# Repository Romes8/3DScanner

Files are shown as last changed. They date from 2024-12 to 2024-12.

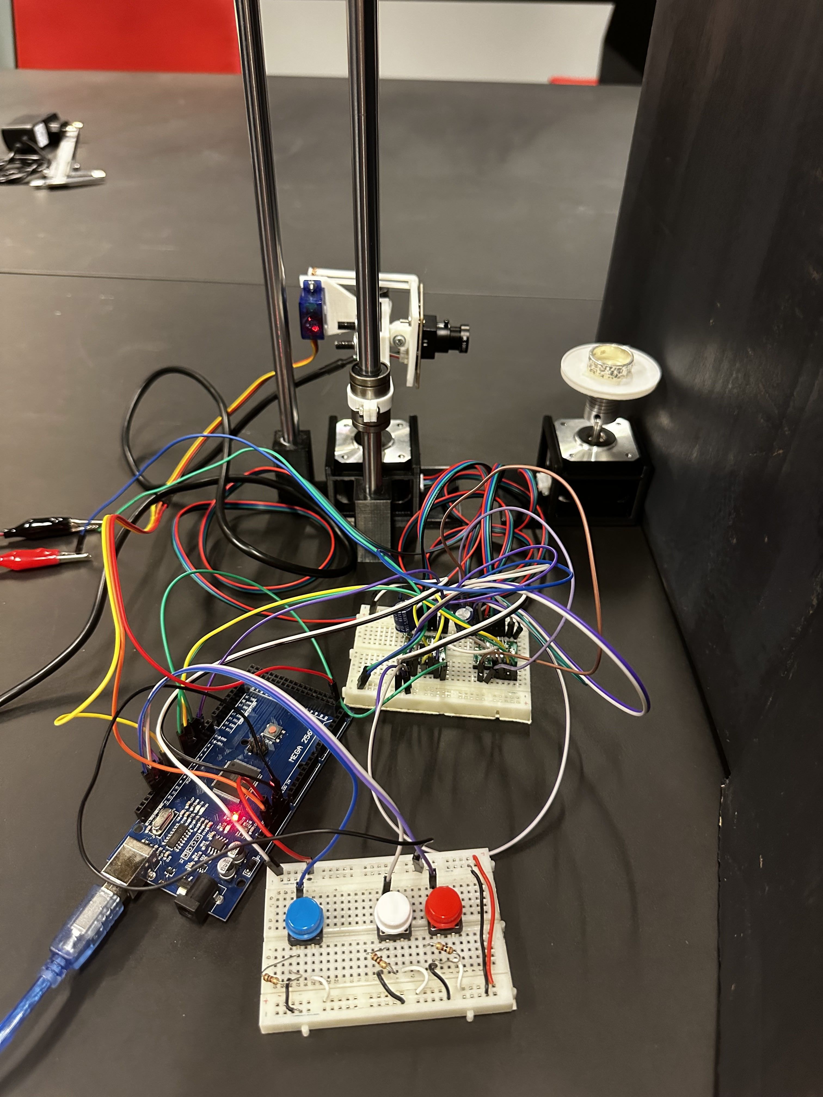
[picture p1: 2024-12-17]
device_images/IMG_8125.jpg

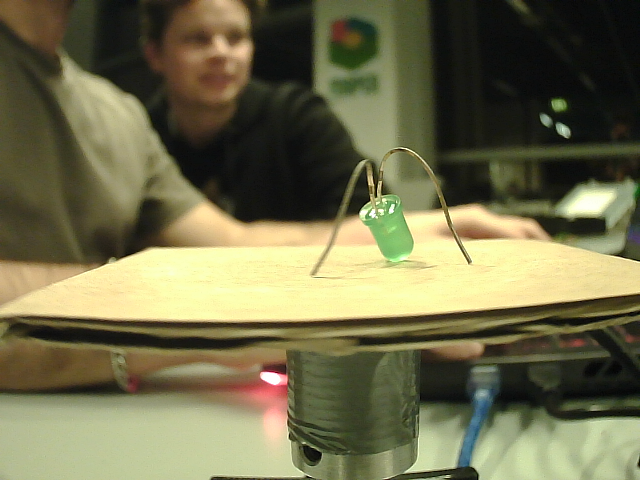
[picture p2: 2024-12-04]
scanned_images/LED/image_20241126-172908.png

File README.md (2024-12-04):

# 3DScanner
Final project for HTMAA 2024  
Overleft report link - https://www.overleaf.com/project/673f16d9a8e7cf6065c0855a

The primary objective of our project, was to design and create a small scale, portable plug and play small scale 3D model scanner. The motivation to create this stems fromour personal interest in 3D printing and miniature models. This paper outlines the steps taken to achieve our goal, discussing different aspects such as the requirements, mechanics, electronics and software used. The results present a successfully designed and executed 3D scanner that was able to scan and reproduce a 3D object.

# How to run 

1. Upload the code into the Arduino using Arduino IDE
2. Turn on "Camera app" on your device
3. Use buttons on the 3DScanner to set the initial scanning position. Adjust the distance to focus on the object
4. Turn off the "camera app"
5. Turn on the camera.py scrpit. Run this in CMD with admin permissions
6. Press the start button on 3D Scanner
7. Verify that the machine starts to move and images are being saved into folder where camera.py script is being saved. 
8. Wait until the 3D Scanner finishes - approx. 8,5 min

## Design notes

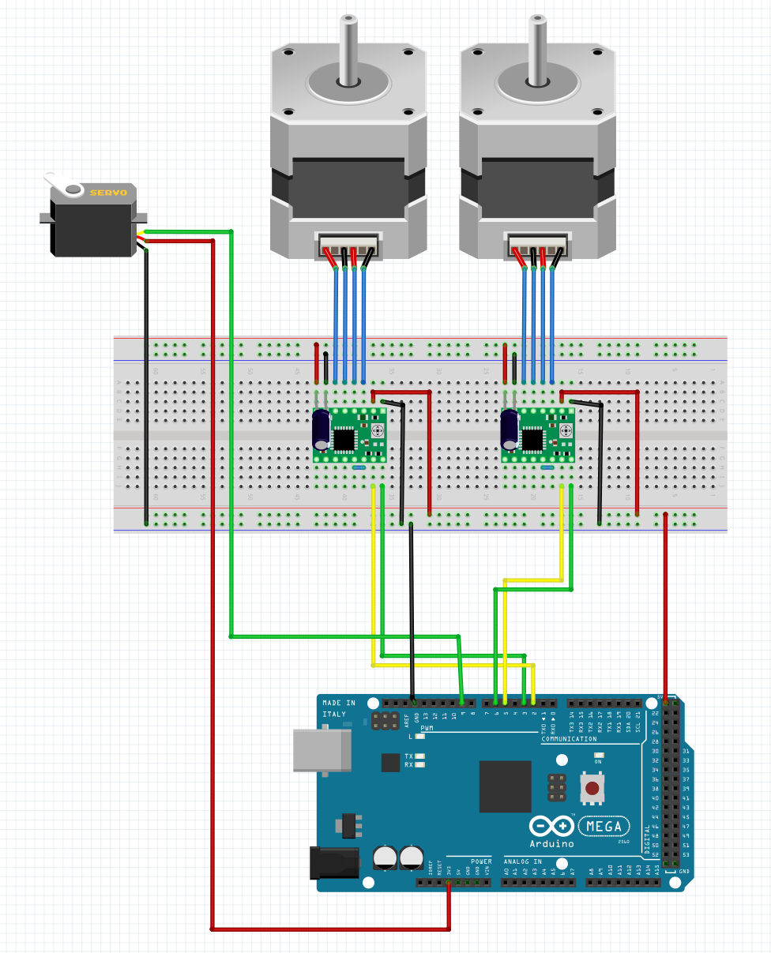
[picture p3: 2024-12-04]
technical_images/arduinoSchematic-scanner.png

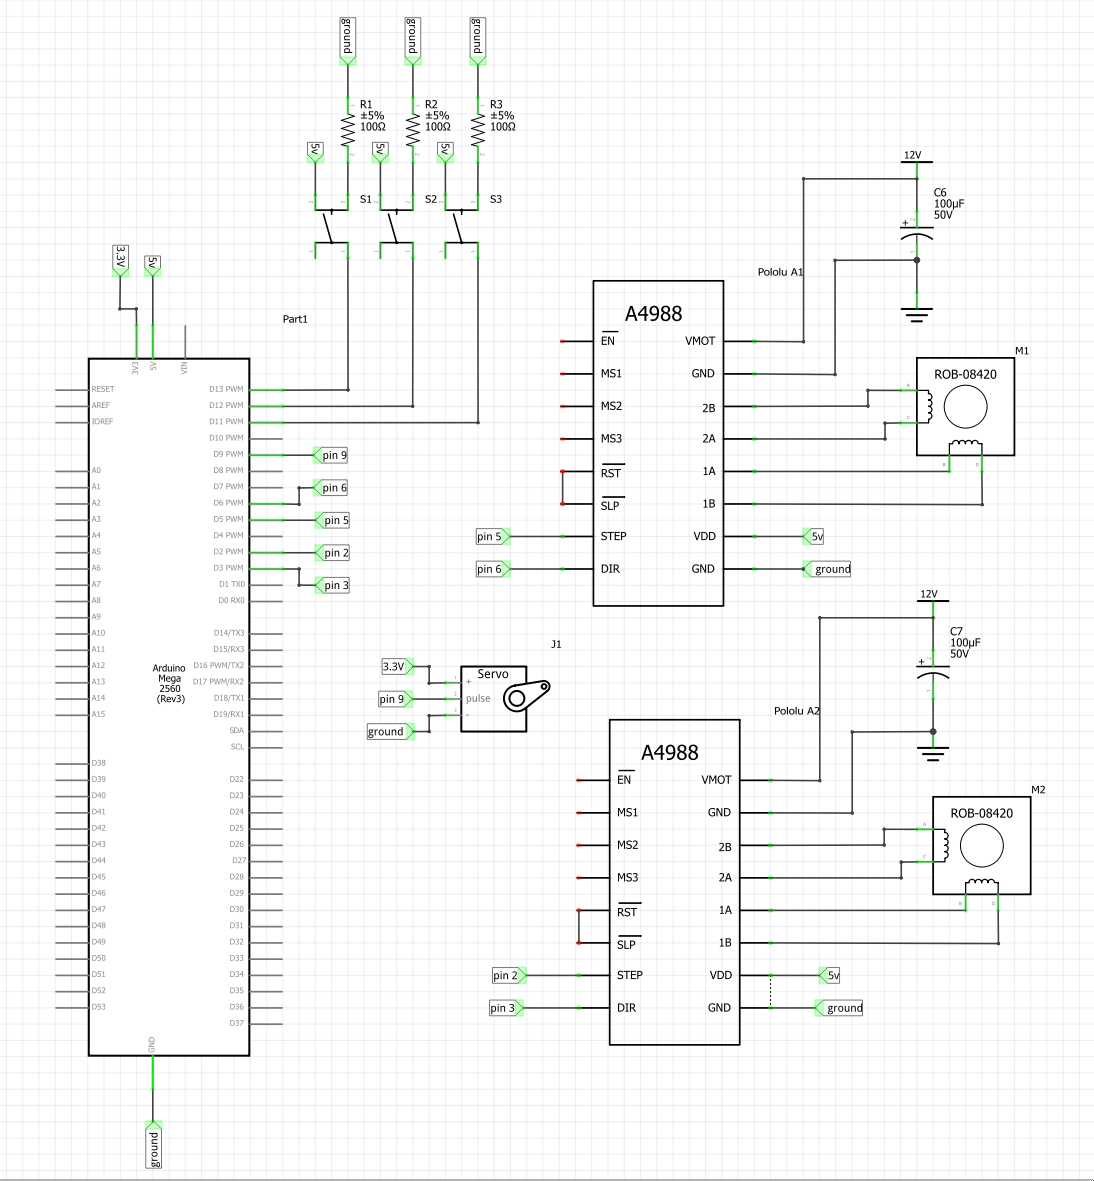
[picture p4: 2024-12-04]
technical_images/schematic-scanner.png

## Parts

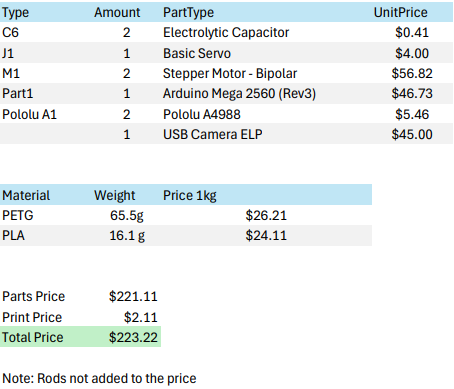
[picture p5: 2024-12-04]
technical_images/BOM-3DScanner.png

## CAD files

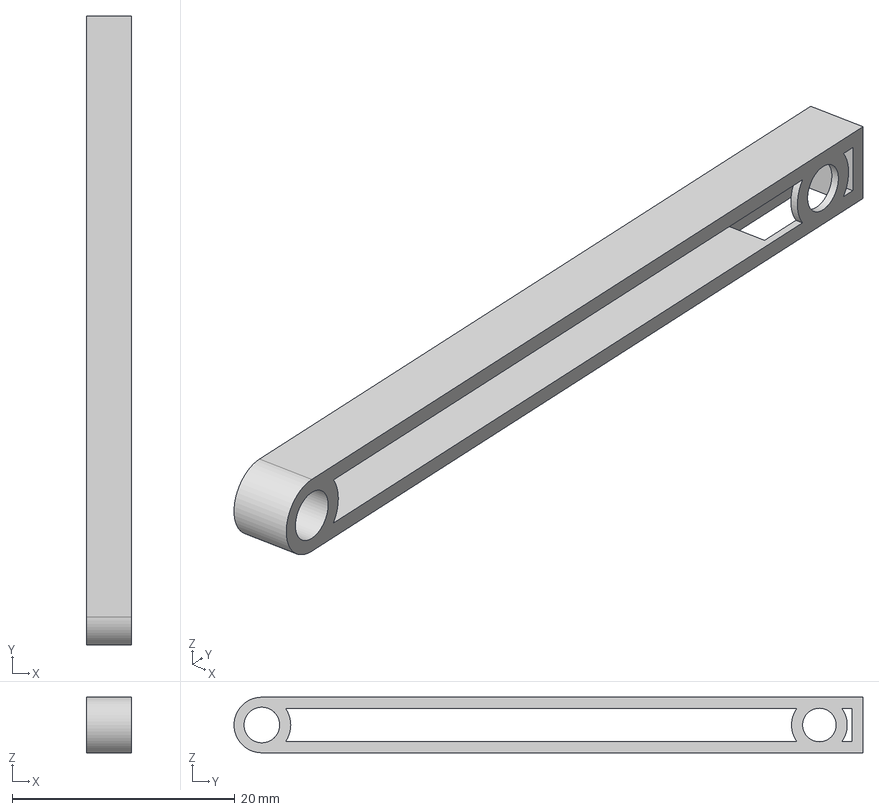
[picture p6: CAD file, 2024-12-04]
3Dmodels/TiltingRod.step
4.00 x 56.5 x 5.00 mm

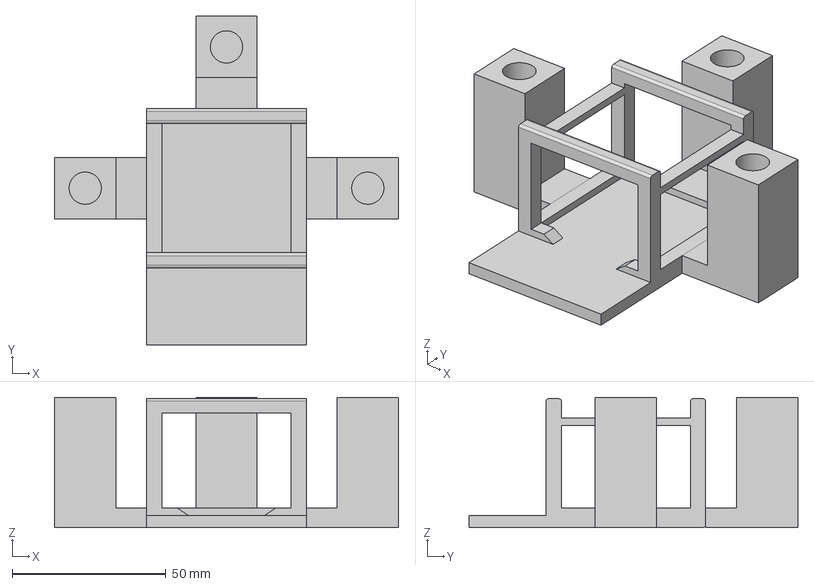
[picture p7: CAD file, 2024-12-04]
3Dmodels/Right motor holderv2.step
112.0 x 107.0 x 42.3 mm

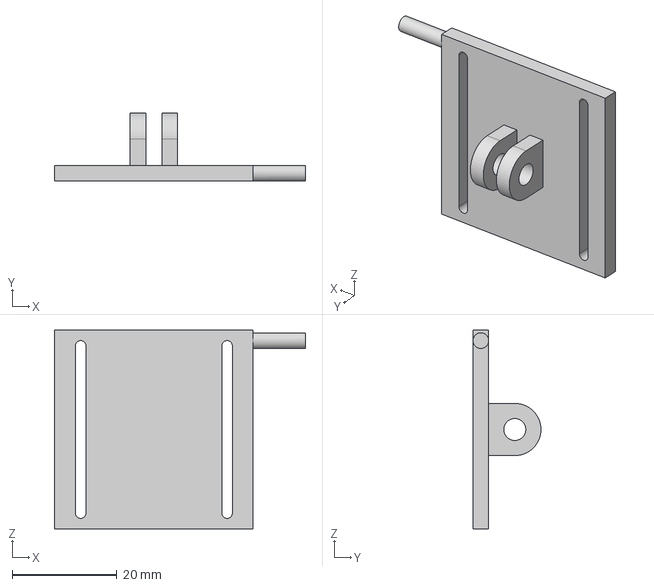
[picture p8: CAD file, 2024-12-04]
3Dmodels/CameraHolder.step
48.0 x 13.0 x 38.0 mm

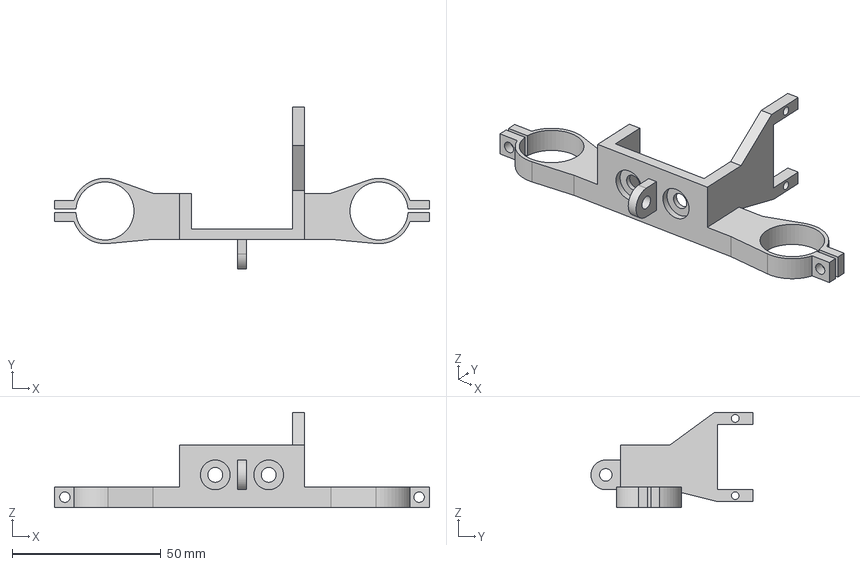
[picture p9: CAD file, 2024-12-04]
3Dmodels/CameraHolderBase.step
126.1 x 54.5 x 32.0 mm

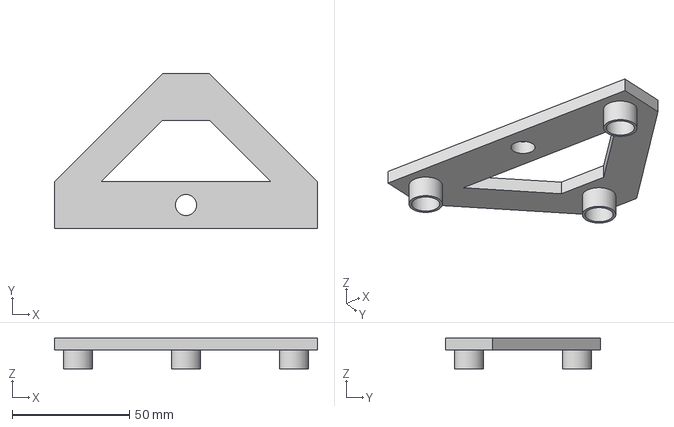
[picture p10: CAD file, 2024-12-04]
3Dmodels/TopHolderv2.step
112.0 x 66.0 x 13.0 mm

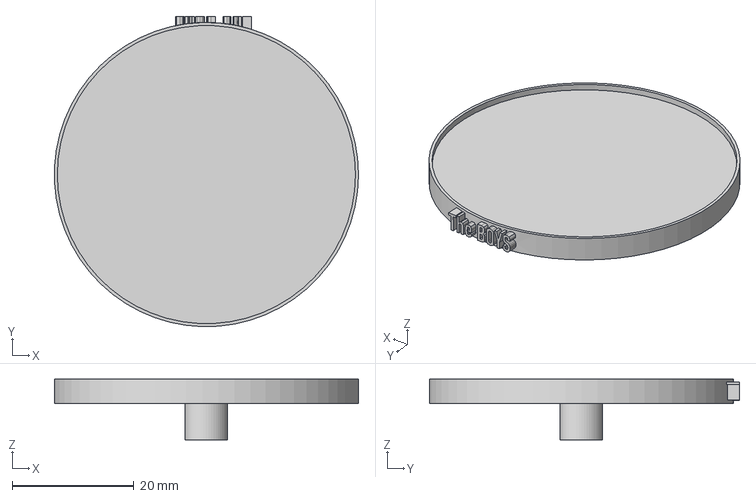
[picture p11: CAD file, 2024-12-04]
3Dmodels/Platform.step
50.0 x 51.0 x 10.0 mm

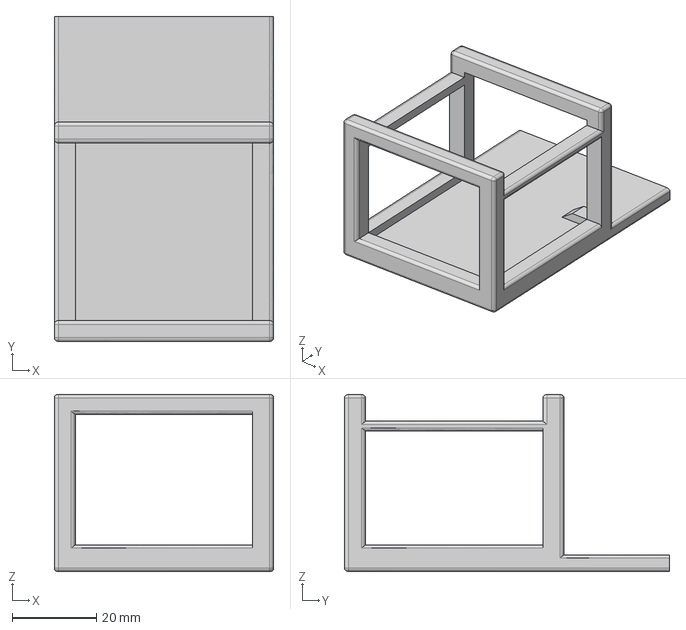
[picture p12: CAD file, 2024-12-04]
3Dmodels/LefMotorHolder.step
52.0 x 77.0 x 42.0 mm

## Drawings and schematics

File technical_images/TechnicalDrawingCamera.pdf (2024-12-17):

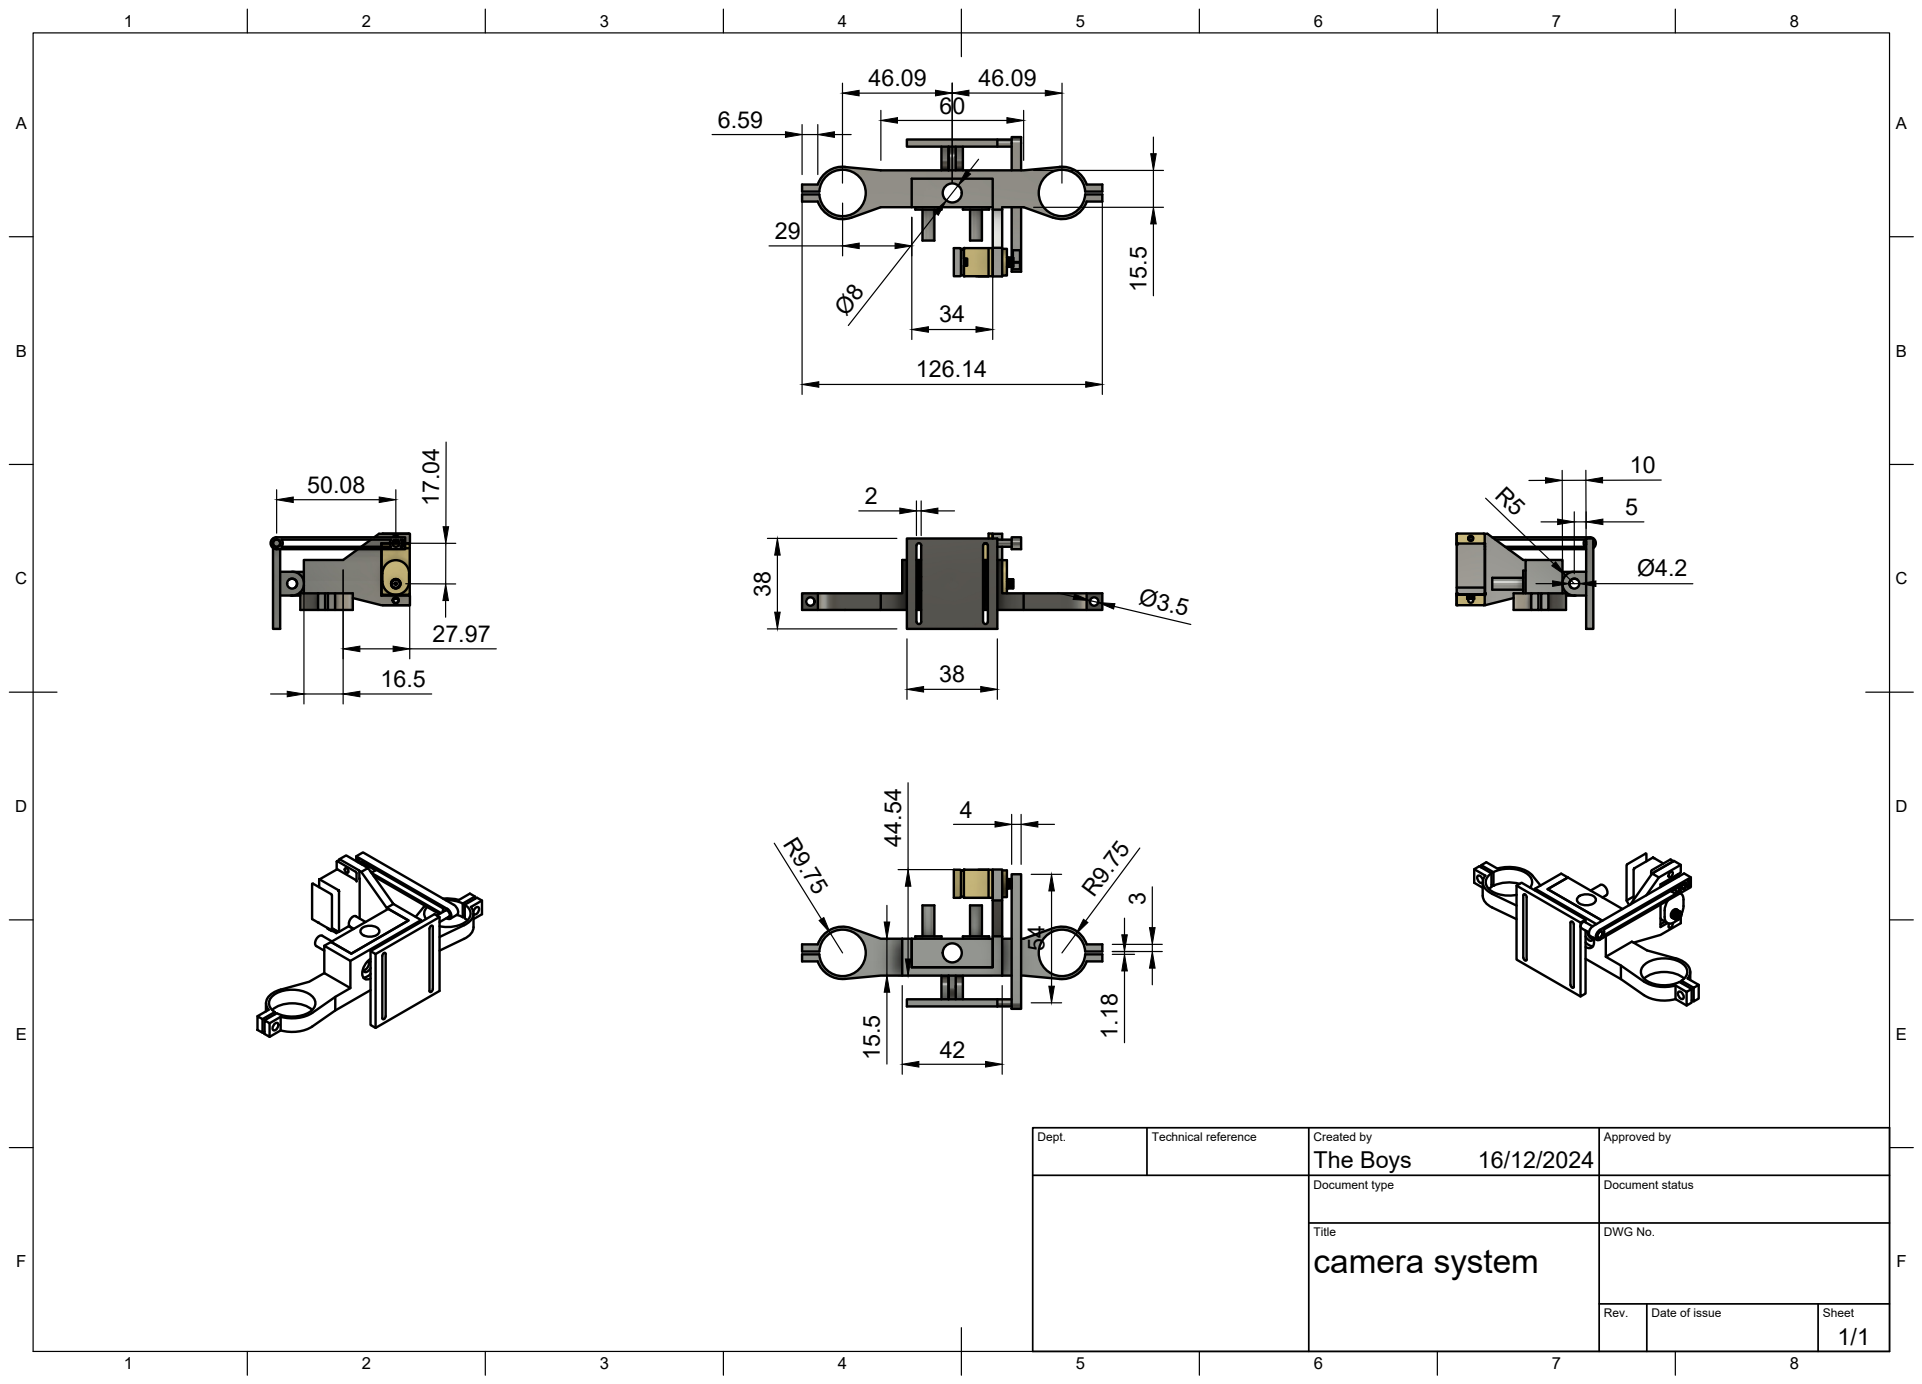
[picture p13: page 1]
Title; DWG No.; Rev.; Date of issue; Sheet; camera system

Dept. | Technical reference | Created by The Boys 16/12/2024 | Approved by

Document type | Document status

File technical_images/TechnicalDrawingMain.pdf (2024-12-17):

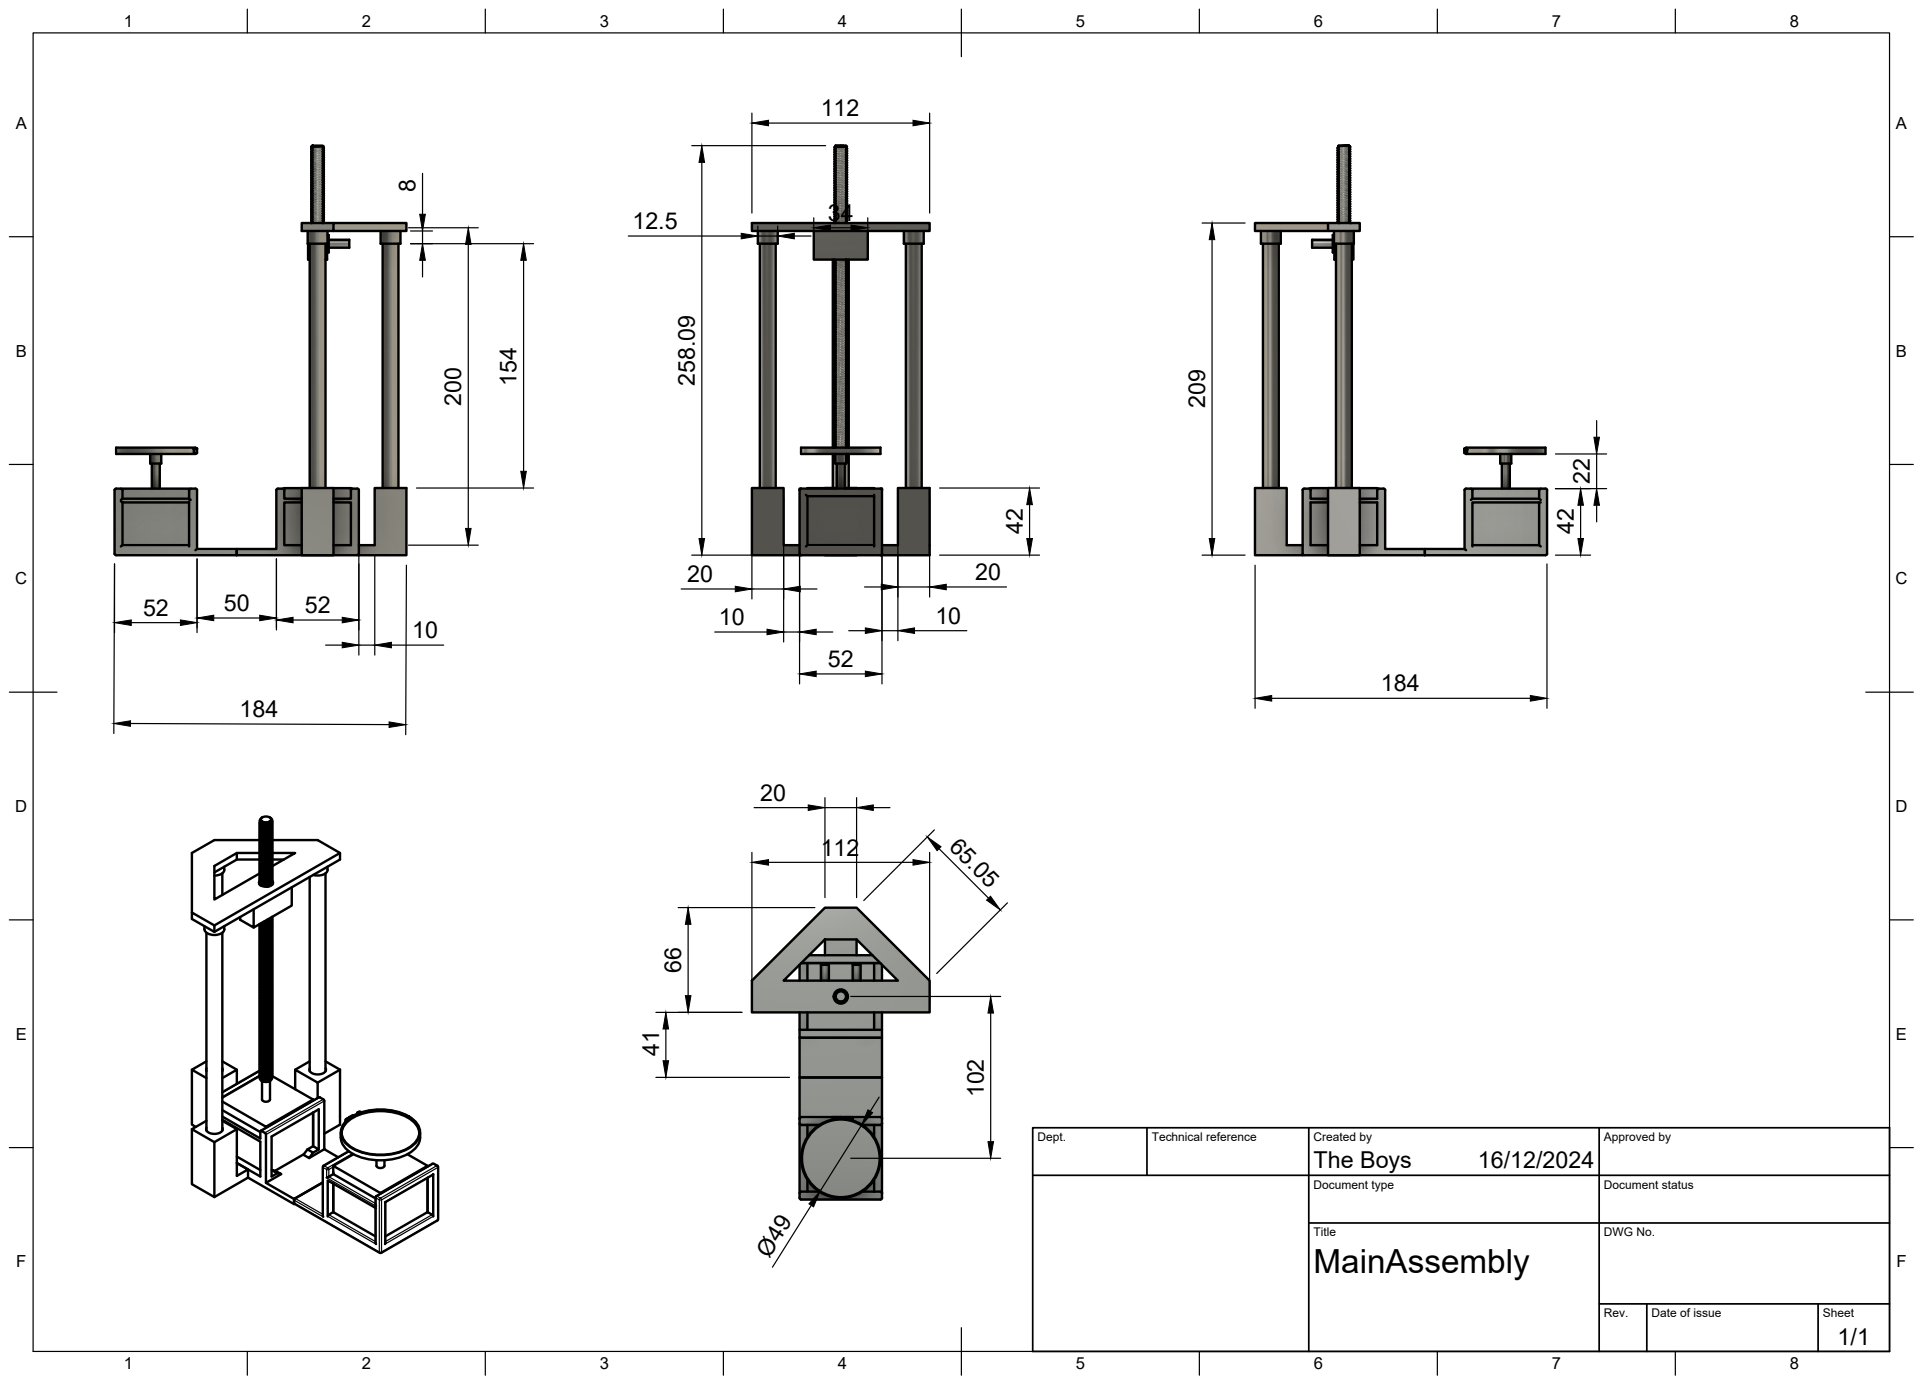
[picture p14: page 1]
Title; DWG No.; Rev.; Date of issue; Sheet; The Boys 258.09

Dept. | Technical reference | Created by 16/12/2024 | Approved by

Document type | Document status

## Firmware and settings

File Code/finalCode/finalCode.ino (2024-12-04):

#include <Servo.h>

// Define pins for both stepper motors
#define stepPin1 2    // First stepper motor step pin
#define dirPin1 3     // First stepper motor direction pin
#define stepPin2 5    // Second stepper motor step pin
#define dirPin2 6     // Second stepper motor direction pin
#define MS1_1 42      // First motor MS1
#define MS2_1 44      // First motor MS2
#define MS1_2 46      // Second motor MS1
#define MS2_2 48      // Second motor MS2

// Servo setup
Servo myservo;  
const int MIN_ANGLE = 75;    // Middle position as minimum
const int MAX_ANGLE = 110;   // Maximum angle
const int START_ANGLE = 75;  // Starting at middle position
int currentServoAngle = START_ANGLE;
int servoAngleChange = 2;

// Steps calculation for 1.8° motor with 1/8 microstepping
const int MICROSTEPS = 8;                              // Using 1/8 microstepping
const int STEPS_PER_REV = 200 * MICROSTEPS;           // Full rotation (1600 steps with 1/8 microstepping)
const int STEPS_18_DEG = (200 * MICROSTEPS * 18) / 360; // 80 steps for 18 degrees with 1/8 microstepping

int segmentCount = 0;
int fullRotationCount = 0;


const int startButton = 13;
const int upButton = 12;
const int downButton = 11;

int start = 0;
int up = 0;
int down = 0;

bool isRunning = false;

void setup() {
  // Stepper setup
  pinMode(stepPin1, OUTPUT); 
  pinMode(dirPin1, OUTPUT);
  pinMode(stepPin2, OUTPUT); 
  pinMode(dirPin2, OUTPUT);

  
  // Servo setup
  myservo.attach(9);
  myservo.write(START_ANGLE);
  
  Serial.begin(9600);
  Serial.println("Starting sequence...");
  delay(1000);  // Initial delay
}

void move_motor(int stepPin, int DirPin, int steps, int speed, int direction) {
  digitalWrite(DirPin, direction);
  Serial.println(steps);

  for(int i = 0; i < steps; i++) {
    digitalWrite(stepPin, HIGH);
    delayMicroseconds(speed);
    digitalWrite(stepPin, LOW);
    delayMicroseconds(speed);
  }
}

void moveServo(int newAngle) {
  if(newAngle != currentServoAngle) {
    Serial.print("Moving servo to angle: ");
    Serial.println(newAngle);
    
    myservo.write(newAngle);
    currentServoAngle = newAngle;
    delay(500); // Allow servo to reach position
  }
}

void loop() {

  start = digitalRead(startButton);
  up = digitalRead(upButton);
  down = digitalRead(downButton);


  if(start == HIGH && !isRunning){
    isRunning = true; 
  }

  if (up == HIGH){
    move_motor(stepPin1, dirPin1, STEPS_18_DEG, 400, HIGH);

  } else if (down == HIGH){
    move_motor(stepPin1,dirPin1, STEPS_18_DEG, 400, LOW);

  } else if (isRunning){

    // Move second motor 18 degrees

    move_motor(stepPin2, dirPin2, STEPS_18_DEG, 1000, HIGH);
    delay(300);

    segmentCount++;
    Serial.println("1");


    // Wait for confirmation message "2"
    bool confirmationReceived = false;
    while (!confirmationReceived) {
      if (Serial.available() > 0) {
        String response = Serial.readStringUntil('\n');
        if (response == "2") {
          confirmationReceived = true;
          Serial.println("Confirmation received, continuing sequence");
        }
      }
      delay(10); 
    }

    // If we completed 360 degrees (20 segments of 18 degrees)
    if(segmentCount >= 20 && fullRotationCount <= 8) {
      Serial.println("360 degrees completed - Moving first motor 360 degrees");

      // Move first motor 360 degrees with 1/8 microstepping
      // Breaking full rotation into 8 segments for smoother movement

      move_motor(stepPin1, dirPin1, STEPS_PER_REV, 500, HIGH);
  

      fullRotationCount++;

      // Move servo down 5 degrees after each full rotation
      
      if(currentServoAngle < MAX_ANGLE && fullRotationCount % 2 == 0) {
        int newAngle = currentServoAngle + servoAngleChange;
        if(newAngle > MAX_ANGLE) newAngle = MAX_ANGLE;
        moveServo(newAngle);
        servoAngleChange = servoAngleChange + 4;
      }

      segmentCount = 0;  // Reset segment counter
      delay(2000);
    }

    delay(1000);  // Wait between movements
  }
}

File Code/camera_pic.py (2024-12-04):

import serial
import cv2
import time

print("Starting the camera app ...")
# Initialize serial connection (adjust 'COM3' and baud rate as needed)
ser = serial.Serial('COM3', 9600, timeout=1)
time.sleep(2)  # Wait for connection to establish

# Initialize camera
cap = cv2.VideoCapture(0)
if not cap.isOpened():
    print("Cannot open camera")
    exit()

while True:
    if ser.in_waiting > 0:
        command = ser.readline().decode('utf-8').strip()
        if command == "1":
            ret, frame = cap.read()
            if ret:
                timestamp = time.strftime("%Y%m%d-%H%M%S")
                filename = f'image_{timestamp}.png'
                cv2.imwrite(filename, frame)
                print(f"Image saved as {filename}")
                ser.write(b"2")

            else:
                print("Failed to capture image")
    
    # Optional: Add a small delay
    time.sleep(0.1)

# Release resources
cap.release()
ser.close()

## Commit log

2024-12-04 Uploaded all files and resources
    [3DScanner.fzz, CameraHolder.step, CameraHolderBase.step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]
2024-12-17 Create device_image folder
2024-12-17 Added device images
2024-12-18 added gif of ring and led
